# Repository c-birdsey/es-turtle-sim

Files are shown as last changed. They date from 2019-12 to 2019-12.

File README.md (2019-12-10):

# Turtle Simulating Robot
### Brandon Choe, Calder Birdsey - December 2019 
## Introduction 

Our main goal for this project was to leverage the software and hardware concepts we learned over the course of this semester to create physical simulation of the [Turtle graphics library](https://docs.python.org/3.3/library/turtle.html?highlight=turtle) in Python. We also wanted to demonstrate a physical representation of the flow from high level commands in our code, to the individual peripherals and components, to a cohesive robot that you could watch perform your inputs in the real world. This connection between hardware and software was a key part of the course, and something we really wanted to explore in our final project.    

The motivation for this project stemmed from our introduction to the computer science major at Middlebury. In both of our intro classes (CSCI101 and CSCI150), we used the Turtle library in Python to practice recursions. Now, as we are wrapping up our penultimate semester at Middlebury, we wanted to return to our humble roots as freshmen and recreate one of the most frustrating parts of our first year, but while tying together everything we learned from this past semester and implementing the relatively simply graphics library in far more complex and challenging manner.        

## Methods 
### Devices and Peripherals   

**Adafruit HUZZAH32 – ESP32 Feather Board**     
This was the microcontroller we used for this project. We initially planned on using the dual cores for multithreading (in order to implement the light sensor) and this informed our decision to use the HUZZAH32. Although our final iteration of the code did not utilize multithreading, the ESP32 Feather was still a great choice because of how simple it was to incorporate it into the breadboard, and the substantial number of GPIO pins.   

**5V Stepper Motor**   
The 5V Stepper Motors are arguably the most important peripherals we used to create our robot, as they offered very precise control over the distance we wanted our robot to travel or turn. The specific motors we used have 513 steps per revolution. Combined with our wheels that had a circumference of 18.78 centimeters, each step was 0.037 centimeters, giving our robot a significant level of precision, which leads to precise drawings.   

**8-Channel Darlington Driver**    
The 8-Channel Darlington Driver was a necessity for our project, because without it, the stepper motors would not have been able to draw enough power to drive our robot. The driver allows the motors to still receive instructions from the ESP32 microcontroller, but supplies the motors with a seperate voltage that is suitable for unipolar stepper motors.       
 
**20mm Metal Caster Bearing Wheel**   
This bearing wheel was essential for giving the robot the ability to reliably change its angle without changing the location of the pen. This feature is obviously very important when designing a robot for drawings, as a typical drawing has dozens of angles, and even a small error would compound into a very visible error if the angles are not precise.    

**Micro Servo**   
We used this peripheral to control the pen_up() and pen_down() commands. The servo simply lifts a small metal hook attached to the pen, lifting the pen off or lowering it onto the canvas. This function is also very important to a drawing robot, as most drawings will not be one continuous line, but will have discontinuities. This feature allows for that possibility.      

**Diffused RED 5mm LED**    
This LED is one of two parts needed for the feature of our robot that checks if the robot is going to drive off the canvas. The LED, using a small paper cone,shines a light underneath the body of the robot, about three centimeters from the front and supplies a continuous and consistent light source for our photoresistor to interact with.   

**Photoresistor**  
The photoresistor reads how much light from the LED is bouncing back from the surface of the canvas onto the photoresistor. Thus, if the robot is moving off the white canvas onto a darker surface, such as a wooden desk or carpeted floor, less light will be measured by the sensor. If the drop in measurement is significant enough (approximately 33% drop), the robot immediately stops its forward movement and waits for a hard reset.   

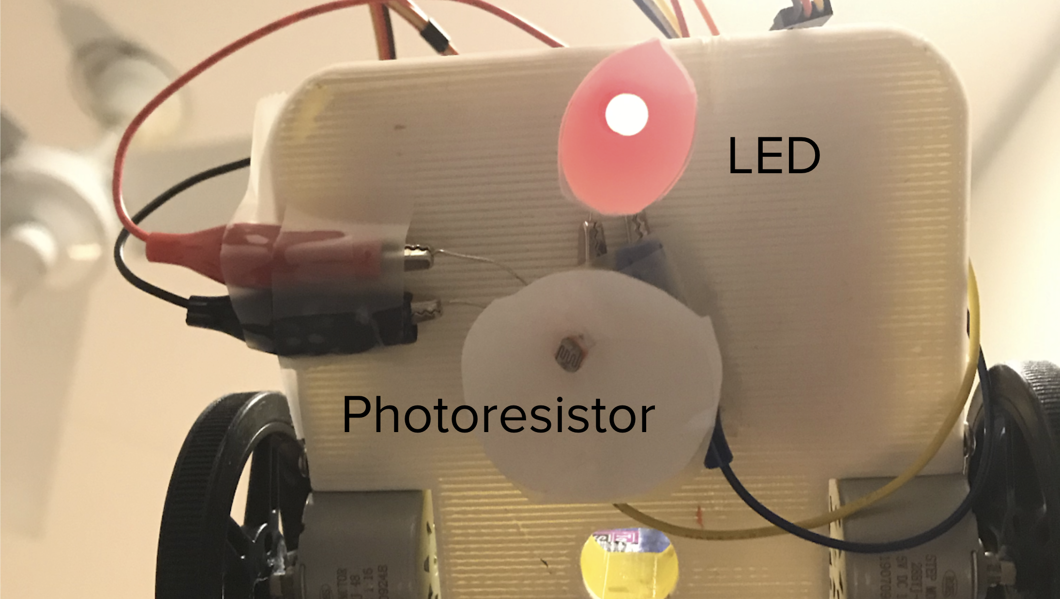
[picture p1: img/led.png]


### Physical Design
For this project, we opted to model and 3D print the majority of the physical robot frame. This allowed for a strong, reproducible design that was efficient and easily tweakable. The frame is fairly simple, with the breadboard and battery balancing the weight on either side. We decided to use two traditional wheels in conjunction with the caster ball bearing, as this allowed for precise turning while drawing. If was quite important for the robot to be able to turn on itself exactly, as it would severely impact the drawing if not. This also informed the location of the pen, which sits directly between the two wheels in a 20mm slot. The servo fits snugly in between the battery pack and pen slot, and like the battery pack and breadboard does not need adhesives of any sort to stay connected to the board. The entire robot frame was printed on a MakerBot Replicator 3D Printer, and the .stl files are included in the repository for this project.   

### Logic and Code Structure
Essentially, our robot relies on a small set of basic commands to execute its drawings. We set out to replicate three simple tasks within the Turtle functionality - movement forward and backward, turning a set number of degrees, and pen position (either up or down). We then broke that into six main functions: forward(dist), backward(dist), right(angle), left(angle), pen_up(), pen_down(). These are what the user can interact with and call to create their drawing. Turning the robot utilizes a helper function to translate the angle given, in degrees, to the number of steps for each wheel, and movement forward and back uses a similar function that translates distance to steps. Both use simple algorithms based on the wheel circumference and steps per rotation of our stepper motors.    

We are also relying on Arduino’s Stepper.h library to create stepper instances, as well as ESP32Servo.h to control and initialize the micro servo (see code snippets below). These two libraries take care of much of the low level initialization, and we could simply interact with the abstracted C++/Arduino syntax. This is all done within the setup() function in Arduino.    

```cpp
// init stepper instances  
Stepper L_wheel(STEPS_PER_REV, 14, 32, 15, 33);     
Stepper R_wheel(STEPS_PER_REV, 27, 12, 13, 21);
``` 

```cpp
//set servo params with standard 50 Hz  
PEN_SERVO.setPeriodHertz(50);  
PEN_SERVO.attach(SERVO_PIN, 1000, 2000);
```

This is also where we are taking an initial reading with the photoresistor to establish a baseline for the canvas color. Within the forward function, we calculate a new canvas reading and compare it to the global baseline - this is how we are implementing the off-canvas detection functionality.   

### User Interface
With this project, the addition of a user interface was initially a stretch goal. As we expected, we weren’t able to develop a UI within our timeline so our “interface” is essentially the Arduino interface. Behavior of the robot can be altered via hard coded instructions in the parent for loop within the Arduino source file and the highest level of abstraction available to a user is simply the Turtle-esque functions we’ve developed. In its current state, our robot executes its drawing directions and then enters into an infinite while loop until powered off, or a new sketch is uploaded (i.e. the ESP32 HUZZAH is reset). As mentioned in the Future Work section, the development of a user interface would be the primary goal if moving forward with this project.   

### Bill of Materials

| Item |Supplier | Quantity | Unit Cost  | Total Cost |
|:--- |:--- |:--- |:--- | ---:|
| HUZZAH32 – ESP32 Feather Board | Adafruit | 1 | $21.95 | $21.95 |
| 20mm Metal Caster Bearing Wheel | Adafruit | 1  | $1.95  | $1.95 |
| 5V Stepper Motor | Adafruit | 2 | $4.95 | $9.90 |
| Skinny Wheel for DC Motor | Adafruit | 2 | $2.50 | $5.00 |
| Micro servo | Adafruit | 1 | $5.95 | $5.95 |
| 4xAA Battery Holder w/switch | Adafruit | 1 | $2.95 | $2.95 |
| Half Sized Breadboard | Sparkfun | 1 | $4.95 | $4.95 |
| 8-Channel Darlington Driver | Adafruit | 1 | $1.95 | $1.95 |
| Photo Cell - CdS Photoresistor | Adafruit | 1 | $0.95 | $0.95 |
| Diffused Red 5mm LED | Adafruit | 1 | $4.00 (25-pack) | $4.00 |
|||||**$59.55**|

## Results   
The end result of our project was very similar to what we envisioned when we were initially ideating what we wanted to create. The two major changes from our earliest designs was a switch from four omnidirectional wheels to two regular wheels and a ball bearing wheel, and the inclusion of the photoresistor and LED.    

This first video shows the precise turns the robot is able to make, the consistency between lines that are meant to be the same length, and the pen_up and pen_down commands. Because this video is from an iteration of the robot without the photoresistor, it runs off the canvas. You can also see the jittery movement of the micro servo, as we were initially having trouble correctly configuring it via the ESP32Servo.h library.     

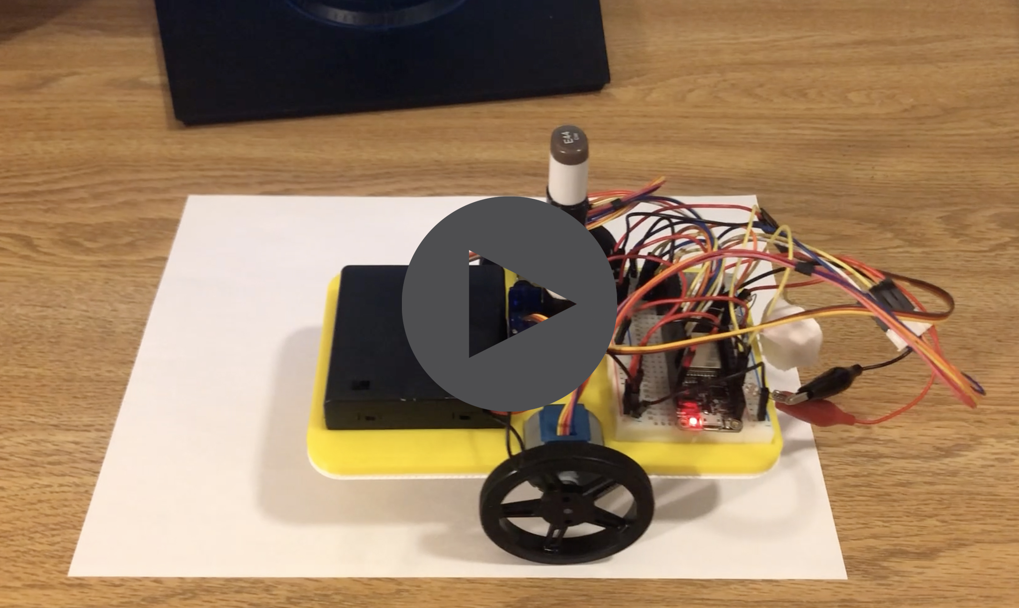
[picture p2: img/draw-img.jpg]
[](https://drive.google.com/file/d/1qrff_zdK6xWhZOJm2RL2-cdg02QwqyaU/view?usp=sharing)

The second video highlights the addition of the photoresistor and LED. In the first run of the robot, it stops once the photoresistor comes off the canvas. Once reset and repositioned, it continues to run, makes a turn, and stops again when going of the canvas. You can also see that we fixed the servo’s jittery behavior.   

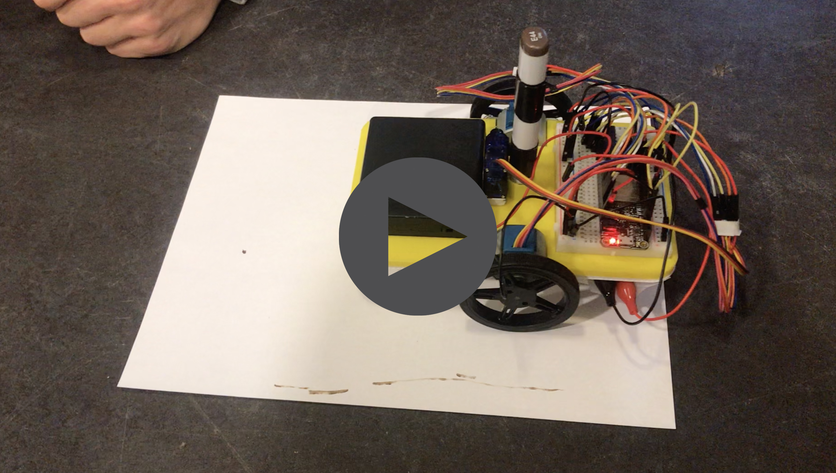
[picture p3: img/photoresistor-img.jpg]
[](https://drive.google.com/file/d/1iHSxn1WZR-QDcf7Hkx0Y760qUZxlPzAe/view?usp=sharing)

## Schedule   
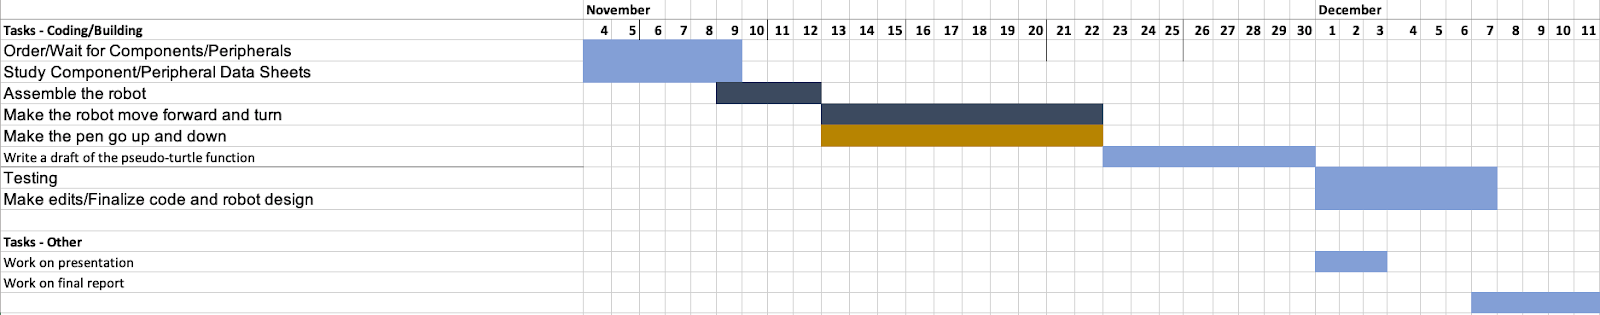
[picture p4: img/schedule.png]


For the most part, we stayed on track with our original schedule. We originally weren’t planning on including the photoresistor and LED to track the robots position, but we were able to get ahead of schedule to create time for the photoresistor and LED. The reason we were able to squeeze more goals into the given timeline of the project is that we overestimated how long it would take to implement basic movement and pen control. These were phases that we thought would be more time consuming and hands-on, and for the most part we were able to assemble the robot smoothly.   

## Issues 
**Wiring the Darlington Driver**  
Initially, we struggled significantly with the wiring of the Darlington Driver and correctly driving the two stepper motors. Because we opted for a more hands-on build (hardwiring the driver rather than using a pre built motor driver breakout board), there was limited documentation online or in datasheets about the correct wiring from our microcontroller output pins to the driver. Eventually, we worked through this process by digging into the inner mechanics of the particular stepper motors we used, and significant trial and error.    

**Throttling 6V Battery Pack**   
This wasn’t a major issue during the project, but it was an aspect of assembly we didn’t fully consider when designing the process. We are using our 6V battery pack to power our microcontroller, LED, photoresistor, two stepper motors, and the micro servo. These peripherals have different ranges of voltage, and so we had to make sure that we were providing correct and safe amounts of power to each.    

**Angle Accuracy**  
Like many of the other projects we saw, we were limited to a certain level of accuracy based on the quality of the hardware we were able to work with, as well as by the fact that this build was indeed a prototype and not assembled with optimum precision. While our stepper motors are fairly accurate for their price, we were not able to get consistent and precise turns from our robot. The turning was also impacted back the surface on which the robot was running on. If on a table or desk with a smooth surface, we often overshoot the programmed turn, and when on carpet or a surface with greater resistance, we were often several degrees below the expected angle.     

## Future Work 
**User Interface and Live Instructions**   
The user interface of the robot, or lack thereof, is what we consider to be the biggest shortcoming of the project. As it is now, to change the instructions for the robot, the user must go into the source code and change the directions in the loop. While we have some layers of abstraction so users don’t have to understand how to use the different libraries we rely on, it is still not very user friendly and assumes a certain level of competence and access to certain resources. It would be far more ideal if we were able to set up a site hosted by the ESP32,  and allow users to provide live instructions to the robot over WiFi. This could be built out to any degree, perhaps even including a Python script and simulation using the Turtle graphics library to see what image you were programming the robot to draw.    

**Preset Letter Functions and Drawings**   
We also think it would be very useful to offer users a preset library of functions for specific drawings or shapes, and perhaps even letters. Figuring out how to draw characters can often be a painful trial and error process, so providing preset function for the letters of the alphabet, and numbers zero through nine could make drawing and writing far easier. It would expand the usability of the robot, and lead to a far better user experience.    

**Calibration**    
A big drawback of the stepper motors we chose for this project is that they can become uncalibrated over time. This means that the distances that users want the robot to move, or the angles they request, will slowly become less and less accurate. Recalibrating the motor can also be a very slow trial and error process, so we think it would be worthwhile to also incorporate an automated process for recalibrating the motors. This would be in the form of some specific, designed drawing pattern that can illuminate the shortcomings of the physical build and provide quicker insight into what needs to be tweaked to regain precision and accuracy.    

**Curves and Circles**    
We chose not to incorporate circles and curves into this iteration of the project because we figured it would be too time consuming to code, as well as outside the range of our (relatively) inexpensive hardware. Technically, it wouldn’t be too difficult of a process (having the two wheels rotate at different speeds) but it would be rather unpredictable and would certainly compound any errors present in the hardware already. That being said, we do acknowledge that circles and curves are important parts of drawing, so we do believe they should be incorporated into future work.     

## References 
- <https://www.vivaxsolutions.com/web/python-turtle.aspx>
- <https://randomnerdtutorials.com/esp32-pir-motion-sensor-interrupts-timers/>
- <https://pimylifeup.com/arduino-light-sensor/>
- <https://wolfpaulus.com/micro-python-esp32/>
- <https://www.espressif.com/sites/default/files/documentation/esp32-wroom-32_datasheet_en.pdf>
- <https://www.arduino.cc/reference/en/#functions>
- <https://github.com/espressif/arduino-esp32>
- <https://docs.espressif.com/projects/esp-idf/en/latest/api-reference/system/intr_alloc.html>
- <https://create.arduino.cc/projecthub/reanimationxp/how-to-multithread-an-arduino-protothreading-tutorial-dd2c37>
- <https://learn.adafruit.com/adafruit-arduino-lesson-16-stepper-motors/breadboard-layout>
- <https://www.arduino.cc/en/Reference/Stepper>
- <https://www.arduinolibraries.info/libraries/esp32-servo>
- <https://docs.python.org/3.3/library/turtle.html?highlight=turtle>

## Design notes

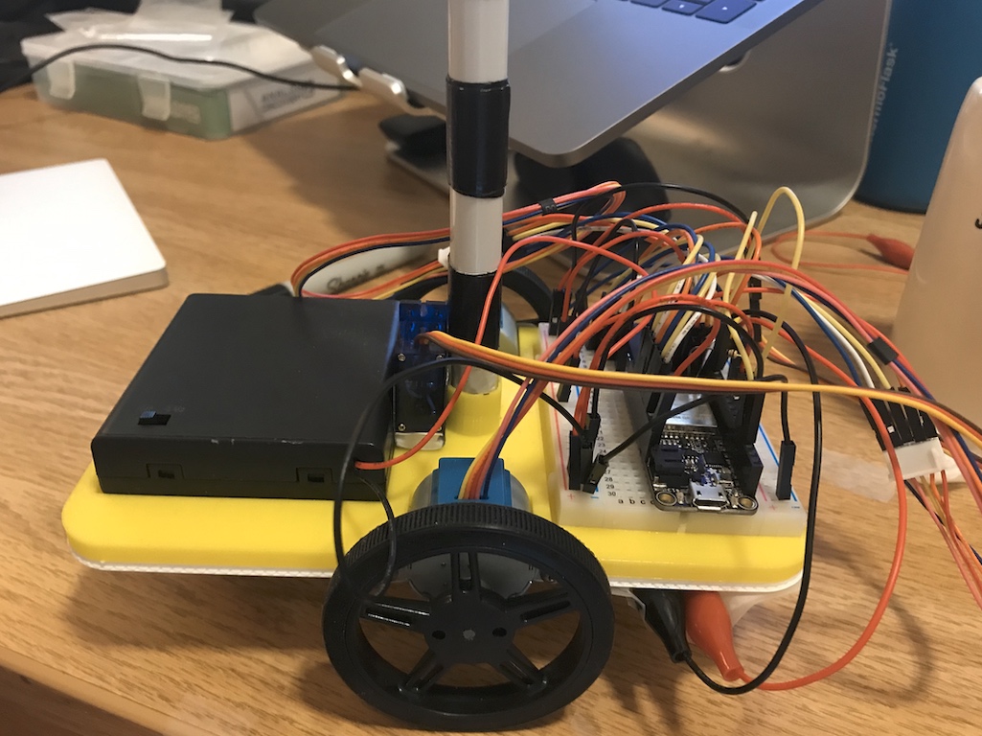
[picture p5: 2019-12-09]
img/robot.jpg

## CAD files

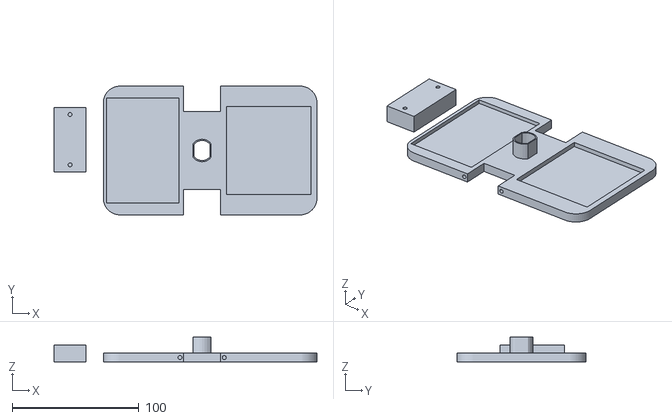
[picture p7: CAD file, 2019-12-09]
stl file/roboto-base.stl
207.6 x 101.6 x 19.7

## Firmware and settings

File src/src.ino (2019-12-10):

/* TURTLE-SIMULATING DRAWING ROBOT

   CSCI435 Embedded Systems
   Middlebury College - Fall 2019
   Authors: Brandon Choe, Calder Birdsey

   Description: Drawing robot simulating Turtle graphics
   library in Python. See full documentation and report at 
   https://c-birdsey.github.io/es-turtle-sim/
*/

/*---------------------------------------------------------------------*/

/* includes */
#include <Stepper.h>
#include <ESP32Servo.h>
#include <Arduino.h>

/* prototypes */
void setup(void);
void loop(void);
void pen_up(void);
void pen_down(void);
void forward(float dist);
void backward(float dist);
void left(int angle);
void right(int angle);
int getSteps(float dist);
int translateAngle(float angle);

/* GLOBALS */
const int STEPS_PER_REV = 513;    //steps per rotation
const int RPM = 50;               //stepper RPMs
const float STEP_ANGLE = 0.689;   //degree per step - technically 0.7 (360 / 513) but tweaked from testing
const float WHEEL_CIRC = 18.787;  //wheel circumference - 18.787cm (7.396in)

/* globals for light sensor reading */
int volatile CANVAS_READING;
int volatile ADJUSTED_READING; 

/* init stepper and servo instances */
Stepper L_wheel(STEPS_PER_REV, 14, 32, 15, 33);
Stepper R_wheel(STEPS_PER_REV, 27, 12, 13, 21);
Servo PEN_SERVO;
int SERVO_PIN = 26;

/* setup function */
void setup() {
  // set speeds for wheels
  L_wheel.setSpeed(RPM);
  R_wheel.setSpeed(RPM);

  //set servo params with standard 50 Hz
  PEN_SERVO.setPeriodHertz(50);
  PEN_SERVO.attach(SERVO_PIN, 1000, 2000);

  // initialize the serial port for debugging 
  Serial.begin(9600);

  //get initial canvas reading
  int vals[20];
  int valSum = 0;
  for (int i = 0; i < 20; i++) {
    vals[i] = analogRead(lightSensorPin);
    valSum += vals[i];
  }
  /* Store initial canvas reading in CANVAS_READING variable and 
   * store adjusted benchmark in ADJUSTED_READING - this is 66% 
   * less than the initial, a threshold determined via trial and 
   * error testing. Only detects movement from light to dark 
   * surfaces (assuming white or near-white background for drawing)
   */
  CANVAS_READING = (valSum / 20);
  ADJUSTED_READING = (CANVAS_READING / 3) * 2; 

 
}

/* parent loop */
void loop() {
  /* basic directions for a 10cm square */
  pen_down();
  forward(10);
  right(90);
  forward(10);
  right(90);
  forward(10);
  right(90);
  forward(10);
  pen_up();
  
  /* entering infinite while after all directions executed */
  while(1){}
}

/*----------------------- HELPER FUNCTIONS ------------------------*/

/* pen_up() - function to move pen off paper via servo control*/
void pen_up() {
  PEN_SERVO.write(80);
  delay(1000);
}

/* pen_down() - function to move pen onto paper via servo control */
void pen_down() {
  PEN_SERVO.write(175);
  delay(1000);
}

/* backward(dist) - function to move robot backward, input distance in cm */
void backward(float dist) {
  int steps = getSteps(dist);
  /* move both wheels a single step at a time */
  for (steps; steps > 0; steps --) {
    L_wheel.step(-1);
    R_wheel.step(1);
    delay(10);
  }
}

/* forward(dist) - function to move robot forward, input distance in cm */
void forward(float dist) {
  int steps = getSteps(dist);
  /* move both wheels a single step at a time */
  for (steps; steps > 0; steps --) {
    /* get new reading from light sensor */
    float measure = analogRead(lightSensorPin); 

    /* compare measurement to adjusted reading var ADJUSTED_READING */
    if((measure - ADJUSTED_READING) > 100) {
      L_wheel.step(1);
      R_wheel.step(-1);
      delay(10);
    } else {
      /* if detected canvas change, enter infinite while loop and wait for restart */
      while(1); 
    }
  }
}

/* right(angle) - function to turn robot to the right, input angle in degrees */
void right(int angle) {
  /* get translation of angle to steps */
  int steps = translateAngle(angle);
  for (steps; steps > 0; steps --) {
    L_wheel.step(-1);
    R_wheel.step(-1);
    delay(10);
  }
}

/* left(angle) - function to turn robot to the left, input angle in degrees */
void left(int angle) {
  /* get translation of angle to steps */
  int steps = translateAngle(angle);
  for (steps; steps > 0; steps --) {
    L_wheel.step(1);
    R_wheel.step(1);
    delay(10);
  }
}

/* getSteps(dist) - function to convert distance to steps using the measured 
 * circumference of wheels and steps per revolution of steppers, returns 
 * step count as integer
 */
int getSteps(float dist) {
  float step_dist = WHEEL_CIRC / STEPS_PER_REV;
  int steps = dist / step_dist;
  return steps;
}

/* translateAngle(angle) - function to convert angle to steps using global
 * STEP_ANGLE which stores steps per degree, returns step count as integer
 */
int translateAngle(float angle) {
  int steps = angle / STEP_ANGLE;
  return steps;
}
